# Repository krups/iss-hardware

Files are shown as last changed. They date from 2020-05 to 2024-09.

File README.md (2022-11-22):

# Kentucky RE-entry Probe Experiment 2
Board files, schematics, DXF, BOM, partslist and documentation for the KREPE-2 mission, part of the KRUPS campaign at the University of Kentucky. Documentation PDF can be found [Flight Computer Hardware Manual](doc/krepe-flight-computer-manual.pdf).

Documentation for the KREPE-1 mission can be found on the krepe1 branch [here](https://github.com/krups/iss-hardware/blob/krepe1/doc/krepe-flight-computer-manual.pdf).

### Board renders
<p>
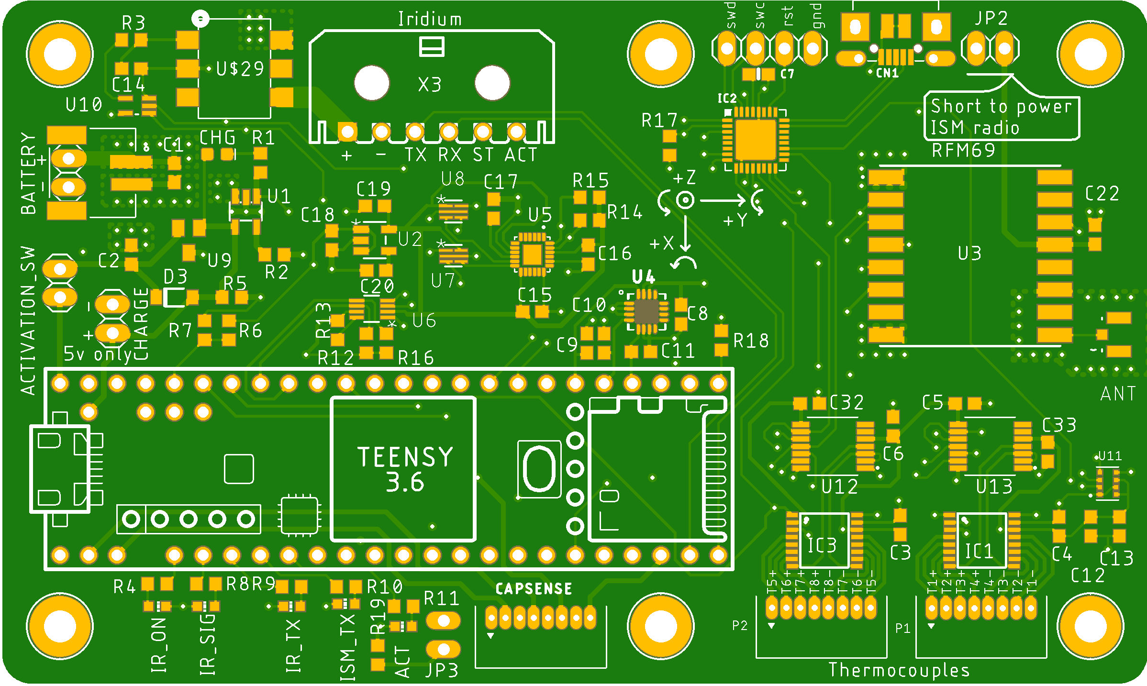
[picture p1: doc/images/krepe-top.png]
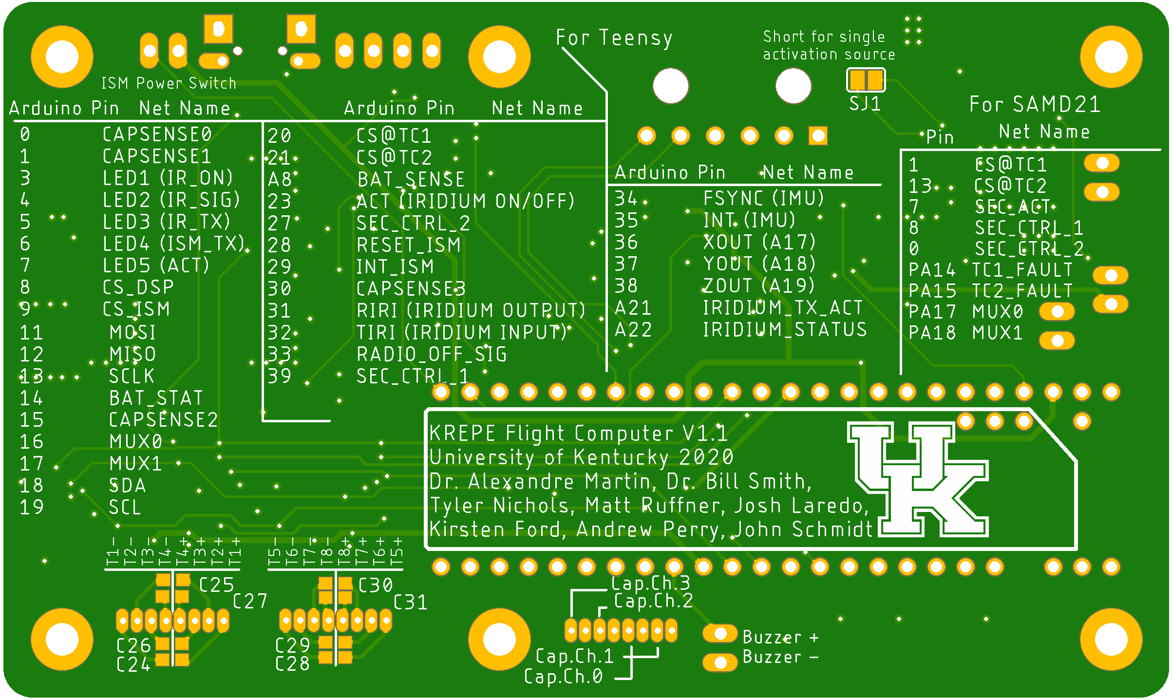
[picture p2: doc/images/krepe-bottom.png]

</p>

### Libraries and datasheets for components
- Thermocouple to digital converter
  -  [MAX31856 Library](https://github.com/adafruit/Adafruit_MAX31856)
  -  [MAX31856 Datasheet](https://datasheets.maximintegrated.com/en/ds/MAX31856.pdf)
- Analog Multiplexer
  - [ADG609BRUZ datasheet](https://www.analog.com/media/en/technical-documentation/data-sheets/ADG608_609.pdf)
- Debug Radio
  - [RFM69HCW](https://www.digikey.com/product-detail/en/sparkfun-electronics/COM-13909/1568-1394-ND/6023504)
- 9-axis IMU
  - [DPE Library](https://github.com/drcpattison/DPEng_ICM20948_AK09916)
  - [Sparkfun Library](https://github.com/sparkfun/SparkFun_ICM-20948_ArduinoLibrary)
  - [Datasheet](https://www.invensense.com/wp-content/uploads/2016/06/DS-000189-ICM-20948-v1.3.pdf)
- Solid state relay
  - [Datasheet](https://www.digikey.com/product-detail/en/panasonic-electric-works/AQV252GAX/255-3375-1-ND/2810282)
- High G Accelerometer
  - [Datasheet](https://www.digikey.com/product-detail/en/analog-devices-inc/ADXL377BCPZ-RL7/ADXL377BCPZ-RL7CT-ND/3678489)
- Safety Co-processor
  - [Datasheet](https://www.digikey.com/product-detail/en/microchip-technology/ATSAMD21E16B-MFT/ATSAMD21E16B-MFTCT-ND/5455793)
  - [Arduino variant reference](https://github.com/adafruit/ArduinoCore-samd/blob/master/variants/trinket_m0/variant.cpp)
 
### Teensy pin assignments wrt. to Arduino 

| Teensy Arduino Pin | Net Name | Notes |
|---|---|---|
| 0 | CAPSENSE 1 |  input, read with ```touchRead(pin)``` |
| 1 | CAPSENSE 0 |  input, read with ```touchRead(pin)``` |
| 3 | LED IRIDIUM ON |  active high |
| 4 | LED IRIDIUM SIGNAL_OK | active high |
| 5 | LED IRIDIUM TRANSMITTING | active high |
| 6 | LED ISM TRANSMITTING | active high |
| 7 | LED ACTIVITY | active high |
| 8			  | CS_DSP		 | active low chip select for DSP310 pressure sensor |
| 9 | CS_ISM | rfm69 chip select |
| 11 | MOSI | |
| 12 | MISO | |
| 13 | SCLK | |
| 14 | BAT_STAT | high when charging |
| 15 | CAPSENSE2 | input, read with ```touchRead(pin)``` |
| 16 | MUX0 | output to analog mux |
| 17 | MUX1 | output to analog mux |
| 18 | SDA | |
| 19 | SCL | |
| 20 | CS@TC1 |  U12 chip select |
| 21 | CS@TC2 |  U13 chip select |
| A8 | BAT SENSE | (A8)  halved by voltage divider |
| 23 | PRI ACT | output to iridium activation 'AND' gate  |
| 24 | BUZZER | buzzer output |
| 25 | TC1 FAULT | (ACTIVE LOW) |
| 26 | TC2 FAULT | (ACTIVE LOW) |
| 27 | SEC CTRL 2 | i/o to safety processor |
| 28 | RESET ISM |  reset to rfm69 |
| 28 | INT ISM |  interrupt from rfm69 |
| 30 | CAPSENSE3 |  input, read with ```touchRead(pin)``` |
| 31 | RIRI | (IRIDIUM OUTPUT) |
| 32 | TIRI | (IRIDIUM INPUT)  |
| 33 | RADIO OFF SIG | pulled high when 3.3v to ism radio is present |
| 34 | FSYNC | IMU sync signal (not necessary for functionality) |
| 35 | INT | IMU interrupt pin (not necessary for functionality) |
| 36 | XOUT | (A17)  high g accel output |
| 37 | YOUT | (A18)  high g accel output |
| 38 | ZOUT | (A19)  high g accel output |
| 39 | SEC CTRL 1 | i/o to safety processor |
| A21 | IRIDIUM TX ACT | iridium output indicating the module is actively transmitting RF |
| A22 | IRIDIUM STATUS |  iridium output indicating an SBD message has arrived |

### Safety processor pin assignments wrt. to Arduino 

The last four pins for the safety processor will need to be added into the board variant file for the trinket m0 since only 5 pins are mapped to physical pads on the current m0 variant.cpp file (or we can make our own arduino board support package ;) )

```SEC CTRL 1``` and ```SEC CTRL 1``` are to be used to coordinate use of the SPI bus so that both the Teensy and safety processor do not drive bus lines to opposite logic levels.

| Safety Processor Arduino Pin|   Net Name                       |                 Note |
|-------------------------|--------------------------|------------------|
| 1                       | CS@TC1                   |    also connected to teensy GPIO              |
| 13                      | CS@TC2                   |    also connected to teensy GPIO              |
| 7                       | SEC ACT                  |     output to activation 'AND' gate             |
| 8                       | SEC CTRL 1               |  i/o with teensy                |
| 0                       | SEC CTRL 2               |  i/o with teensy                |
| PA14                    | TC1 FAULT                |         input        |
| PA15                    | TC2 FAULT                |    input            |
| PA17                    | MUX0                     |       need to use i/o with teensy to avoid collisions on SPI bus           |
| PA18                    | MUX1                     |        need to use i/o with teensy to avoid collisions on SPI bus         |

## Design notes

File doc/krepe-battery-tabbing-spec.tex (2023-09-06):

\documentclass{article}
\usepackage[utf8]{inputenc}

\title{KREPE2 Battery Tabbing Process Specification and Acceptance Testing}
\author{Matt Ruffner, Kirsten Ford}
\date{}

\usepackage{url}
\usepackage{float}
\usepackage{tikz}
\usepackage{natbib}
\usepackage{graphicx}
\usepackage{listings}
\usepackage{subcaption}
\usepackage{fullpage}
\usepackage{hyperref}
\usepackage{pdfpages}
\hypersetup{
    colorlinks=true,
    linkcolor=blue,
    filecolor=magenta,      
    urlcolor=cyan,
}

\begin{document}

\maketitle
\tableofcontents
\listoffigures
\listoftables
\newpage

%%%%%%%%%%%%%%%%%%%%%%%%%%%%%%%%%%%%%%%%%%%%%%%%%%%%%%%%%%%%%%%%%%%%%%%%%%%%%%%%%%%%%%%%%
%%%%%%%%%%%%%%%%%%%%%%%%%%%%%%%%%%%%%%%%%%%%%%%%%%%%%%%%%%%%%%%%%%%%%%%%%%%%%%%%%%%%%%%%%
%%%%%%%%%%%%%%%%%%%%%%%%%%%%%%%%%%%%%%%%%%%%%%%%%%%%%%%%%%%%%%%%%%%%%%%%%%%%%%%%%%%%%%%%%
%%%%%%%%%%%%%%%%%%%%%%%%%%%%%%%%%%%%%%%%%%%%%%%%%%%%%%%%%%%%%%%%%%%%%%%%%%%%%%%%%%%%%%%%%
\section{Introduction}
This document outlines the procedures and verifications done to ensure the integrity of the spot welds used to attach tabs to the 18650 cells for the KREPE-2 mission. The procedures and specifications in this documents have been written to adhere to the guidelines of NASA battery tabbing and specification document \textit{\textbf{PRC-0009 Rev. D}}. According to this document, ``A Welding Procedure Specification (WPS) shall be qualified for each unique weld type to be produced by conforming to the requirements below, before the production welds are made." The WPS for tabbing the KREPE-2 batteries is defined in the following section. 

\section{Battery Acceptance Testing}

1 minute per axis

used spectrum that was already qualified by JSC document, help with reflight

Batteries were vibration tested at Yokohama facilities at the cell level on each axis. Capacity and open circuit voltage (OCV) were recorded before (see Tab. \ref{tab:acc1}) and after testing (see Tab. \ref{tab:acc2}) to ensure no cells were damaged during vibration. Six cells can be seen on the shaker table in the cell mounting form in Fig. \ref{fig:cell-setup}.

\begin{figure}[H]
\centering
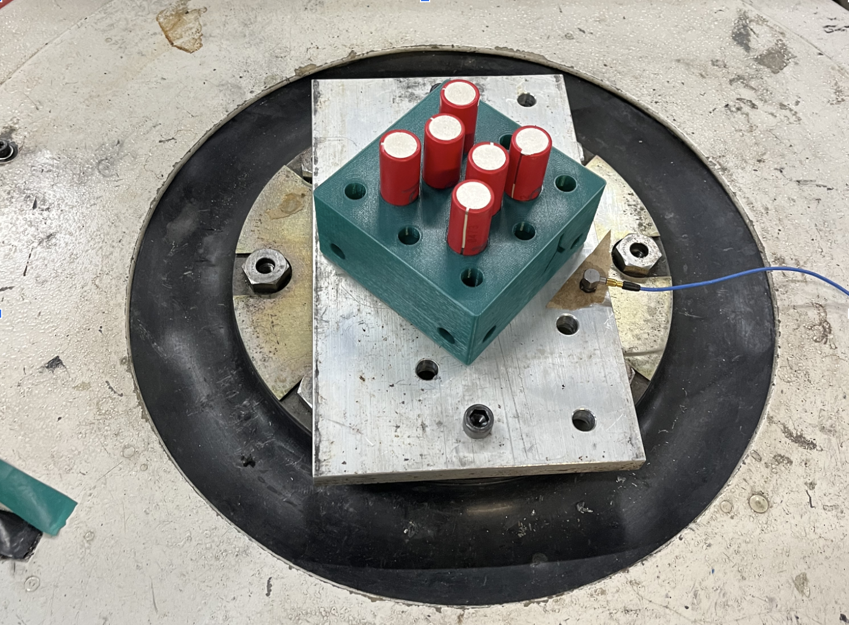
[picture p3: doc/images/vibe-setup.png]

\caption{Six cells in the 3D printed battery holder, mounted to the Yokohama shaker table.}
\label{fig:cell-setup}
\end{figure}

\begin{table}[H]
    \centering
    \caption{Capacity and voltage measurements made before vibration testing.}
    \begin{tabular}{llll}
        \textbf{Cell \#} & \textbf{OCV before vibe (V)} & \textbf{Capacity before vibe (mAh)} & \textbf{Pass vibe visual inspection? y/n} \\ \hline
        1 & 4.14 & 3138 & y \\ 
        2 & 4.15 & 3100 & y \\ 
        3 & 4.15 & 3151 & y \\ 
        4 & 4.14 & 3132 & y \\ 
        5 & 4.16 & 3124 & y \\ 
        6 & 4.16 & 3099 & y \\ 
        7 & 4.14 & 3109 & y \\ 
        8 & 4.14 & 3091 & y \\ 
        9 & 4.15 & 3159 & y \\ 
        10 & 4.14 & 3148 & y \\ 
        11 & 4.17 & 3123 & y \\ 
        12 & 4.17 & 3102 & y \\ 
        13 & 4.13 & 3093 & y \\ 
        14 & 4.14 & 3091 & y \\ 
        15 & 4.15 & 3139 & y \\ 
        16 & 4.15 & 3158 & y \\ 
        17 & 4.17 & 3111 & y \\ 
        18 & 4.17 & 3103 & y \\ 
        19 & 4.13 & 3107 & y \\ 
        20 & 4.13 & 3110 & y \\ 
        21 & 4.14 & 3095 & y \\ 
        22 & 4.13 & 3116 & y \\ 
        23 & 4.15 & 3169 & y \\ 
        24 & 4.15 & 3141 & y \\ 
        25 & 4.15 & 3161 & y \\ 
        26 & 4.15 & 3162 & y \\ 
        27 & 4.17 & 3117 & y \\ 
        28 & 4.17 & 3109 & y \\ 
        29 & 4.17 & 3099 & y \\ 
        30 & 4.17 & 3126 & y \\ 
        31 & 4.14 & 3096 & y \\ 
        32 & 4.14 & 3065 & y \\ 
        33 & 4.14 & 3102 & y \\ 
        34 & 4.14 & 3119 & y \\ 
        35 & 4.15 & 3153 & y \\ 
        36 & 4.15 & 3142 & y \\ 
    \end{tabular}
    \label{tab:acc1}
\end{table}

\begin{table}[H]
    \centering
    \caption{Capacity and voltage measurements after vibration testing. The differences in measured capacity from before and after vibration shows that all cells passed the acceptance test.}
    \begin{tabular}{lllll}
        \textbf{Cell \#} & \textbf{OCV after vibe (V)} & \textbf{Capacity after vibe (mAh)} & \textbf{\%diff OCV} & \textbf{\%diff capacity} \\ \hline
        1 & 4.15 & 3117 & 0\% & 1\% \\ 
        2 & 4.15 & 3110 & 0\% & 0\% \\ 
        3 & 4.15 & 3108 & 0\% & 1\% \\ 
        4 & 4.14 & 3163 & 0\% & -1\% \\ 
        5 & 4.16 & 3191 & 0\% & -2\% \\ 
        6 & 4.16 & 3179 & 0\% & -3\% \\ 
        7 & 4.14 & 3169 & 0\% & -2\% \\ 
        8 & 4.14 & 3168 & 0\% & -2\% \\ 
        9 & 4.15 & 3123 & 0\% & 1\% \\ 
        10 & 4.15 & 3124 & 0\% & 1\% \\ 
        11 & 4.17 & 3111 & 0\% & 0\% \\ 
        12 & 4.17 & 3114 & 0\% & 0\% \\ 
        13 & 4.14 & 3125 & 0\% & -1\% \\ 
        14 & 4.14 & 3183 & 0\% & -3\% \\ 
        15 & 4.14 & 3131 & 0\% & 0\% \\ 
        16 & 4.15 & 3142 & 0\% & 1\% \\ 
        17 & 4.17 & 3141 & 0\% & -1\% \\ 
        18 & 4.17 & 3121 & 0\% & -1\% \\ 
        19 & 4.14 & 3103 & 0\% & 0\% \\ 
        20 & 4.13 & 3121 & 0\% & 0\% \\ 
        21 & 4.14 & 3168 & 0\% & -2\% \\ 
        22 & 4.14 & 3140 & 0\% & -1\% \\ 
        23 & 4.15 & 3101 & 0\% & 2\% \\ 
        24 & 4.15 & 3132 & 0\% & 0\% \\ 
        25 & 4.15 & 3146 & 0\% & 0\% \\ 
        26 & 4.15 & 3141 & 0\% & 1\% \\ 
        27 & 4.17 & 3161 & 0\% & -1\% \\ 
        28 & 4.17 & 3164 & 0\% & -2\% \\ 
        29 & 4.17 & 3168 & 0\% & -2\% \\ 
        30 & 4.17 & 3176 & 0\% & -2\% \\ 
        31 & 4.14 & 3180 & 0\% & -3\% \\ 
        32 & 4.14 & 3154 & 0\% & -3\% \\ 
        33 & 4.14 & 3111 & 0\% & 0\% \\ 
        34 & 4.14 & 3118 & 0\% & 0\% \\ 
        35 & 4.15 & 3105 & 0\% & 2\% \\ 
        36 & 4.15 & 3114 & 0\% & 1\% \\ 
    \end{tabular}
    \label{tab:acc2}
\end{table}

\section{Welding Process Specification}

\subsection{Equipment}

The battery welder used is a kit welder\footnote{\url{https://malectrics.eu/product/diy-arduino-battery-spot-welder-prebuilt-kit-v3/}} powered by a 12000mAh 3S LiPo battery. The full welding setup including battery, weld controller, and probes can be seen in Fig.~\ref{fig:welder}. Detailed information about the welding equipment is shown in Table~\ref{tab:weldequip}. 

Not every detail from the \textit{\textbf{PRC-0009 Rev. D}} spec is able to be replicated with this setup, including the ability to measure the down force of the probes on to working surface. In order to make sure that the welds stay consistent, a \textit{trained hand} method is used. This ensures that the person performing the resistance spot welds on the flight cells is the same person performing the welds for the weld process verification. In both scenarios this person is Matt Ruffner.

\begin{figure}[h!]
\centering

\caption{Battery tab welding equipment. Battery (left) attaches to the weld controller (center) and allows weld parameters to be changed for use with the welding probes (right).}
\label{fig:welder}
\end{figure}

\begin{table}
\centering
\caption{Resistance spot welding weld schedule}
\label{tab:weldequip}
\begin{tabular}{|l l|}
\hline
\multicolumn{2}{|l|}{\textbf{Equipment Identification}} \\
Owner / location &  KRUPS, RGAN 110 \\
Power supply & MaxAmps 3S 12000 mAh LiPo \\
Weld controller serial number & sw-pbkit-v4 \\
Weld head / model & SeeSii 2021 \\
Interconnecting cable & 8 AWG, 6 in \\
&\\
\hline
\multicolumn{2}{|l|}{\textbf{Battery}} \\
Manufacturer & Sanyo \\
Type / size & NCR18650B-H07XA \\
Material type & Lithium ion battery \\
&\\
\hline
\multicolumn{2}{|l|}{\textbf{Connecting Material}} \\
Manufacturer & SeeSii \\
Type & Nickel \\
Thickness / width & 1.5"L x 0.355"W x 0.005"T \\
&\\
\hline
\multicolumn{2}{|l|}{\textbf{Electrodes}} \\
Manufacturer & SeeSii \\
Material & Copper \\
Distance between electrode tips & 0.2 in \\
Contact tip surface shape & round \\
Electrode tip size & 0.059 in. diameter\\
&\\
\hline
\multicolumn{2}{|l|}{\textbf{Welding electrode configuration and setup}} \\
Number of pulses &  1 \\
%Squeeze time      & 1 second \\
%Upslope duration & N/A \\
Pulse duration & 10 ms \\
%Downslope & 0 ms \\
%Hold time & 500 ms \\
%Negative Electrode Force &1 lbs \\
%Positive Electrode Force &1 lbs\\
%Pull force & ??\\
\hline
\end{tabular}
\end{table}

\subsection{Process}

say certified operator instead of trained hand

add reference to section 4 table

A tab weld consists of two separate weld instances, yielding 4 weld points, or ``nuggets", on each tab. There are two types of packs required for this mission. The 3S1P pack requires standard tab-to-battery welds, while the 1S3P pack requires tab-to-battery welds as well as tab-to-tab welds.

To qualify both of these processes, plug pull out tests will be done for tabs attached to other tabs and tabs attached to batteries. In both scenarios, success is determined by plug pullout, signifying that the weld is indeed stronger than the original material by itself.

\begin{enumerate}
\item Cut 4 pieces of tab material 1.5" long
\item Mark 4 points 0.2 in apart to weld at on each tab
\item Ensure the battery powering the welder is charged and its voltage is greater than 11.1 V
\item Initialize the weld controller and select 10ms weld pulse duration
\item Stabilize the battery and pin the tab with one electrode
\item Press the other weld tip to the battery
\item Repeat weld for second weld on a given tab. 
\end{enumerate}

\section{Weld Verification}

change language to "it can be seen"

As per PRC-0009, 15 sets of example welds are the minimum test batch size. To this end, tabs were attached to both the positive and negative ends of two Sanyo cells. There are 16 total welds resulting (in groups of 4 spot welds for each tab attachment point).

Figure~\ref{fig:stabilized-tab} shows a tab sitting on top of the first cell, prior to tabbing. After this, 4 points were marked on the tab to indicated where the welds were to be placed. After the markings are placed, the weld tips are pressed to the tab with a moderate amount of force by hand. The weld controller senses this connection and triggers a weld 4 seconds after the tips are touched to the tab. After both welds have been done on a single tab (producing 4 weld nuggets), the tab looks like that shown in Fig.~\ref{fig:post-weld}.

\begin{figure}[h]
\centering

\caption{Nickel tab stabilized on top to cell prior to welding.}
\label{fig:stabilized-tab}
\end{figure}

\begin{figure}[h]
\centering
\begin{subfigure}{0.6\textwidth}

\caption{After both welds have been performed on the tab. You can see the silver sharpie locater markings underneath the weld to help guide the placement of the weld tips during the welding process.}
\label{fig:post-weld}
\end{subfigure}
\hfill
\begin{subfigure}{0.3\textwidth}

\caption{Pliers were used to pull the welded tab off of the battery at a right angle to the surface of the weld.}
\label{fig:pull-config}
\end{subfigure}
\caption{Result of resistance spot welding using our weld controller and the configuration of the destructive peel test.}
\end{figure}

After all 4 tabs are attached to the two cells with a total of 16 weld nuggets, the peel test proceeds. The peel test consists of holding the cell in the upright position and using a pair of pliers to pull the tab at a 90 degree angle to the working surface (the plane of the welds). This configuration is shown in Fig.~\ref{fig:pull-config}.

Using this configuration, the destructive peel test continued. The tabs were pulled at right angles until the tab cam free from the battery. The results of the 4 peel tests are shown in Figs.~\ref{fig:peel-1}, \ref{fig:peel-2}, \ref{fig:peel-3}, and \ref{fig:peel-4}. As you can see, all 16/16 weld nuggets proved stronger than the tab, and the 4 peel tests resulted in 100\% plug pullout. 

\begin{figure}[H]
\centering

\begin{subfigure}{0.3\textwidth}

\caption{Tab 1, test cell 1.}
\label {fig:peel-1}
\end{subfigure}
\hfill
\begin{subfigure}{0.3\textwidth}

\caption{Tab 2, test cell 1.}
\label {fig:peel-2}
\end{subfigure}
\\
\begin{subfigure}{0.3\textwidth}
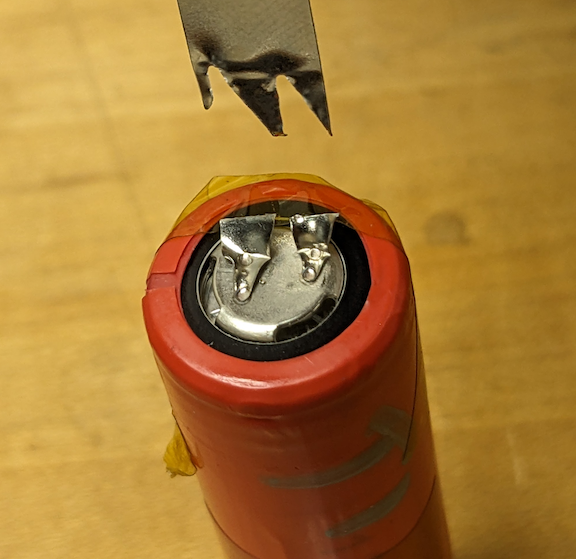
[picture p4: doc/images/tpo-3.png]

\caption{Tab 1, test cell 2.}
\label {fig:peel-3}
\end{subfigure}
\hfill
\begin{subfigure}{0.3\textwidth}
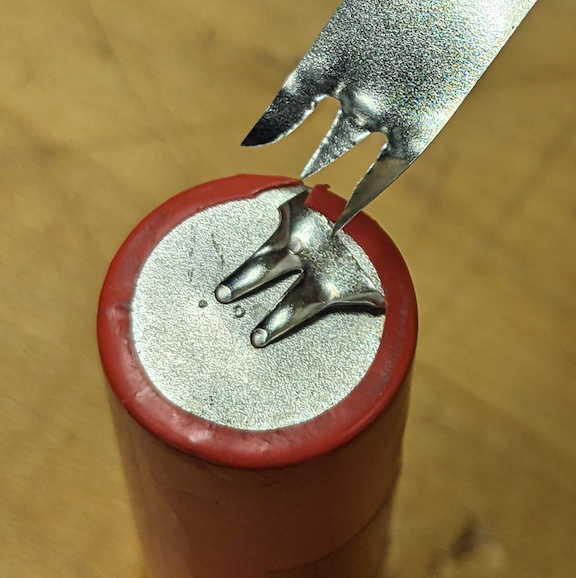
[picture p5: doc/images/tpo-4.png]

\caption{Tab 2, test cell 2.}
\label {fig:peel-4}
\end{subfigure}
\caption{Results of plug pull out tests on the sample batch of welds.}
\end{figure}

\subsection{Weld Process Verification Summary}
Using the welding setup shown in Fig.~\ref{fig:welder}, 16 weld nuggets were created and tested to destruction with a peel test. For all 16 nuggets, plug pullout occurred. This confirms the strength of the welding process specified in this document.

\section{Battery Tabbing Arrangement}

The KREPE-2 capsules have 2 battery packs with 3 cells each. One is a 3.7V pack with the cells tabbed in parallel, and another 11.1V pack with the cells tabbed in series. Figures \ref{fig:parallel-pack} and \ref{fig:series-pack} show the arrangement of the tabs on the cells for the 3.7V and 11.1V pack, respectively.

\begin{figure}[H]
\centering

\begin{subfigure}{0.45\textwidth}
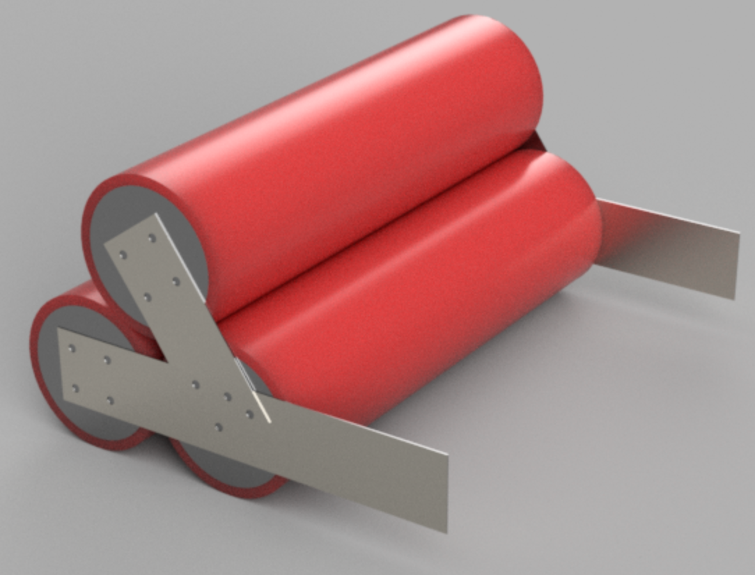
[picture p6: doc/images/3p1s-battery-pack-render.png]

\caption{Rendering of 3.7V 3P1S battery pack}
\label {fig:parallel-pack}
\end{subfigure}
\hfill
\begin{subfigure}{0.45\textwidth}
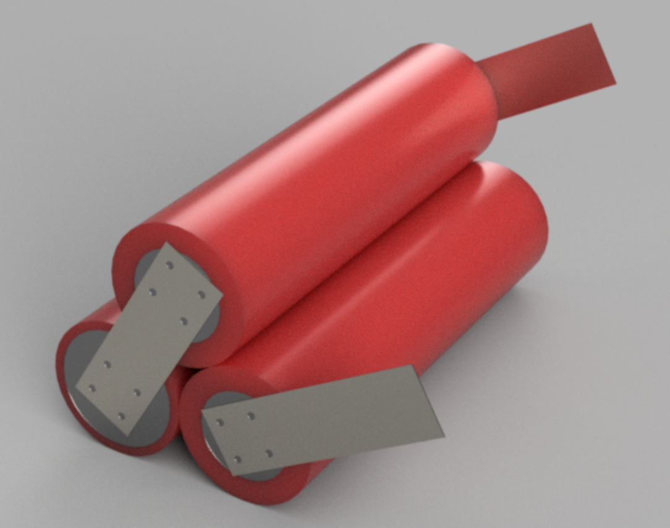
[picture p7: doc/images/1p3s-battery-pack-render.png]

\caption{Rendering of 11.1V 1P3S battery pack}
\label {fig:series-pack}
\end{subfigure}

\end{figure}

The tabbing material is made of nickel strips measuring $0.005$ inches thick and $0.355$ inches wide and cut to length before being attached to the batteries. Dimensional drawings showing weld spacing and tab dimensions for both packs can be found in Figs. \ref{fig:1s3p_drawing} and \ref{fig:3s1p_drawing}.

\appendix

add drawing number

add approval for drawings

\section{Battery Pack Drawings}
Dimensions in inches.
\begin{figure}
\centering

\caption{3S1P pack drawing.}
\label{fig:3s1p_drawing}
\end{figure}

\begin{figure}
\centering

\caption{1S3P pack drawing.}
\label{fig:1s3p_drawing}
\end{figure}

\end{document}

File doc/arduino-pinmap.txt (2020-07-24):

Arduino Pin     Net

Teensy 3.5
0               CAPSENSE0
1               CAPSENSE1
3               LED_IRIDIUM_ON
4               LED_IRIDIUM_SIGNAL_OK
5               LED_IRIDIUM_TRANSMITTING
6               LED_ISM_TRANSMITTING
7               LED_ACTIVITY
8		CS_DSP
9               CS_ISM
11              MOSI
12              MISO
13              SCLK
14              BAT_STAT
15              CAPSENSE2
16              MUX0
17              MUX1
18              SDA
19              SCL
20              CS@TC1
21              CS@TC2
A8              BAT_SENSE (A8)
23              PRI_ACT (IRIDIUM ON/OFF)
24              BUZZER
25              TC1_FAULT (ACTIVE LOW)
26              TC2_FAULT (ACTIVE LOW)
27              SEC_CTRL_2
28              RESET_ISM
28              INT_ISM
30              CAPSENSE3
31              RIRI (IRIDIUM OUTPUT)
32              TIRI (IRIDIUM INPUT)
33              RADIO_OFF_SIG
34              FSYNC (IMU)
35              INT (IMU)
36              XOUT (A17)
37              YOUT (A18)
38              ZOUT (A19) 
39              SEC_CTRL_1        
A21             IRIDIUM_TX_ACT
A22             IRIDIUM_STATUS

Safety Processor (ATSAMD21E16B)
1               CS@TC1
13              CS@TC2
7               SEC_ACT
8               SEC_CTRL_1
0               SEC_CTRL_2
PA14            TC1_FAULT
PA15            TC2_FAULT
PA17            MUX0
PA18            MUX1

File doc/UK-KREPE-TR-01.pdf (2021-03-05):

# UK-KREPE-TR-01

Matt Ruffner
2/12/2021

Verification of battery protection circuitry
Functional verification of the battery protection circuitry (BPC) was performed by shorting the battery pack together downstream of the BPC. The results of this test are shown in Fig. 1. The top trace shows the pack voltage prior, during, and after a short circuit scenario. The bottom trace is the current draw from the pack. As you can see, after 6 milliseconds, the BPC engages and cells are disconnected from the output and current draw from the pack drops to zero amps. In addition, a low voltage cutoff test was performed on the KREPE Experiments with the battery protection circuitry in place that verifies electrical systems are disabled when battery voltage reaches less than 3.3 volts.

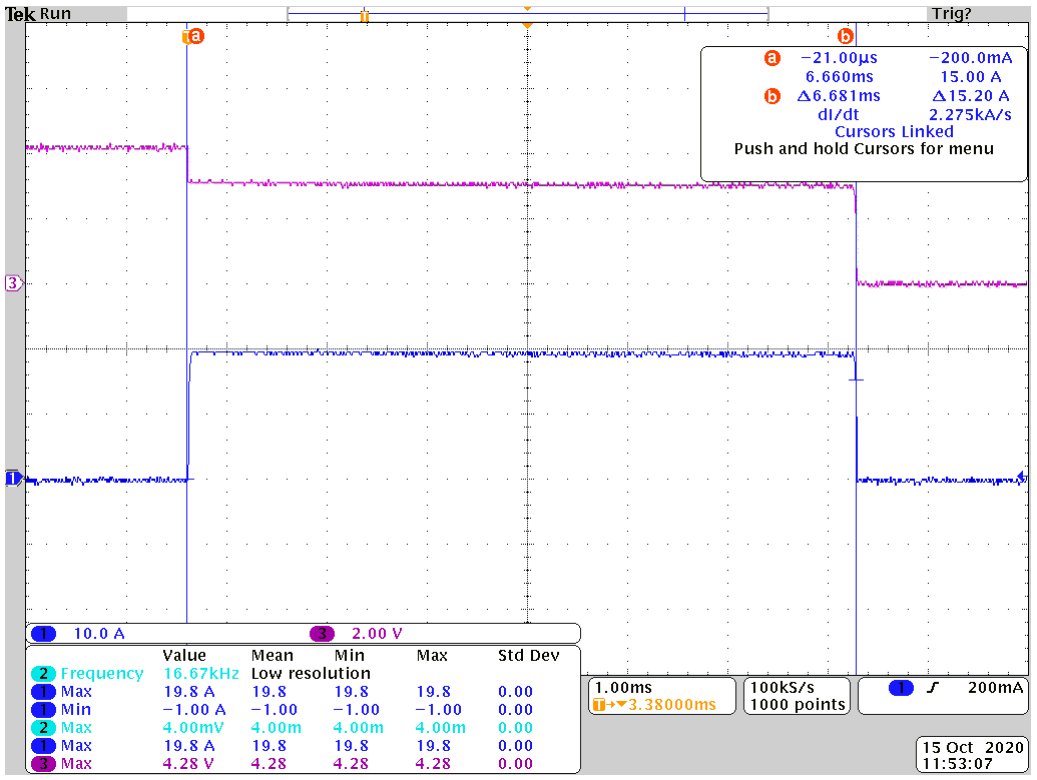
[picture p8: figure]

Figure 1: Overcurrent protection engaging on the battery protection circuitry.

Functional testing before and after vibration
After this initial visual inspection, functional testing was performed before and after vibration testing at MSFC. All KREPE Experiments were tested to ensure that they power up into the dormant state upon removal of the pull tab. The test to ensure a capsule starts and goes into dormant mode consists of pulling the pull-tab and listening for startup beeps. Then, listen for an additional two minutes and ensure no activation beep is detected. In addition to not hearing the activation beep, it was additionally confirmed that the capsules did not activate because no iridium packets were received.

Table 1: Functional test before vibe
Part # | Serial # | Date | Pass/Fail | Initial
KREPE-001 | 001 | 1/30/2021 10:44 EST | PASS | MR
KREPE-001 | 002 | 1/30/2021 10:51 EST | PASS | MR
KREPE-002 | N/A | 1/30/2021 11:11 EST | PASS | MR

Table 2: Functional test after vibe
Part # | Serial # | Date | Pass/Fail | Initial
KREPE-001 | 001 | 2/4/2021 15:37 EST | PASS | MR
KREPE-001 | 002 | 2/4/2021 10:51 EST | PASS | MR
KREPE-002 | N/A | 2/4/2021 11:00 EST | PASS | MR

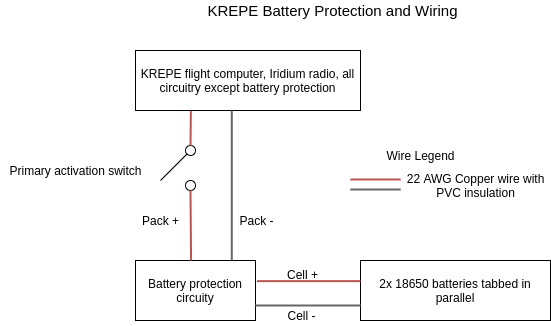
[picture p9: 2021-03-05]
doc/images/krepe-electrical-overview.png

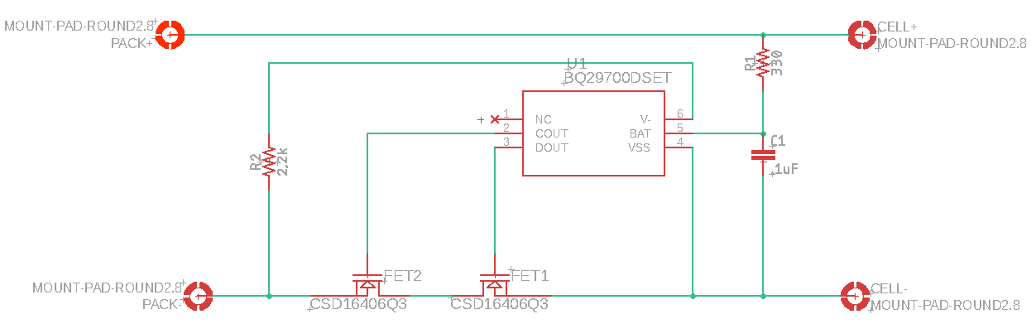
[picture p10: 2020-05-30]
doc/images/battery_protection_schematic.png

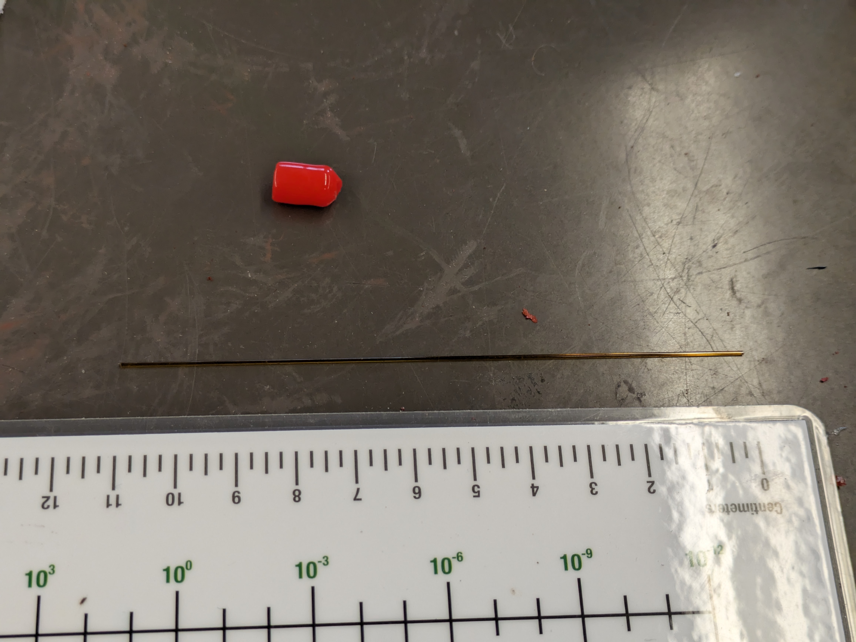
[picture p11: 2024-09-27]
doc/images/krepe2build/spectrometer4.jpg

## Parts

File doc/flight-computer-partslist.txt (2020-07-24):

Partlist

Exported from flight-computer.sch at 7/23/20 8:11 PM

EAGLE Version 9.6.2 Copyright (c) 1988-2020 Autodesk, Inc.

Assembly variant: 

Part          Value                Device                 Package                   Library                 Sheet

ACTIVATION_SW                      PINHD-1X2              1X02                      pinhead                 3
ANT           U.FL-R-SMT-1(10)     U.FL-R-SMT-1(10)       CONN_R-SMT-1(10)          ufl                     4
BATTERY       2 PIN JST            S2B-PH-SM4-TB(LF)(SN)  JST_S2B-PH-SM4-TB(LF)(SN) S2B-PH-SM4-TB_LF__SN_   3
C1            10uF                 C-EUC0603              C0603                     rcl                     3
C2            1uF                  C-EUC0603              C0603                     rcl                     3
C3            0.1uF                C-USC0603              C0603                     adafruit                2
C4            0.1uF                C-USC0603              C0603                     adafruit                2
C5            0.1uF                C-USC0603              C0603                     adafruit                2
C6            0.1uF                C-USC0603              C0603                     adafruit                2
C7            1uF                  CAP_CERAMIC0603_NO     0603-NO                   microbuilder            5
C8            10uF                 C-USC0603              C0603                     adafruit                1
C9            0.01uF               C-USC0603              C0603                     adafruit                1
C10           0.01uF               C-USC0603              C0603                     adafruit                1
C11           0.01uF               C-USC0603              C0603                     adafruit                1
C12           0.1uF                C-EUC0603              C0603                     rcl                     4
C13           0.1uF                C-EUC0603              C0603                     rcl                     4
C14           0.1uF                C-USC0603              C0603                     adafruit                3
C15           0.1uF                C-EUC0603              C0603                     rcl                     1
C16           0.1uF                C-EUC0603              C0603                     rcl                     1
C17           0.1uF                C-EUC0603              C0603                     rcl                     1
C18           0.1uF                C-USC0603              C0603                     rcl                     3
C19           2.2uF                C-USC0603              C0603                     rcl                     3
C20           0.01uF               C-USC0603              C0603                     rcl                     3
C22           1uF                  C-EUC0603              C0603                     rcl                     4
C24           0.01uF               C-USC0603              C0603                     adafruit                2
C25           0.01uF               C-USC0603              C0603                     adafruit                2
C26           0.01uF               C-USC0603              C0603                     adafruit                2
C27           0.01uF               C-USC0603              C0603                     adafruit                2
C28           0.01uF               C-USC0603              C0603                     adafruit                2
C29           0.01uF               C-USC0603              C0603                     adafruit                2
C30           0.01uF               C-USC0603              C0603                     adafruit                2
C31           0.01uF               C-USC0603              C0603                     adafruit                2
C32           0.1uF                C-USC0603              C0603                     adafruit                2
C33           0.1uF                C-USC0603              C0603                     adafruit                2
CAPSENSE      53048-0810           53048-0810             53048-0810                con-molex-picoblade     4
CHARGE                             PINHD-1X2              1X02                      pinhead                 3
CHG           RED                  LED-RED0603            LED-0603                  SparkFun-LED            3
CN1           4U#20329             USB_MICRO_20329_V2     4UCONN_20329_V2           microbuilder            5
D3            MBR120               MBR120                 SOD123FL                  gsynth                  3
H1            MOUNT-PAD-ROUND2.8   MOUNT-PAD-ROUND2.8     2,8-PAD                   holes                   1
H2            MOUNT-PAD-ROUND2.8   MOUNT-PAD-ROUND2.8     2,8-PAD                   holes                   1
H3            MOUNT-PAD-ROUND2.8   MOUNT-PAD-ROUND2.8     2,8-PAD                   holes                   1
H4            MOUNT-PAD-ROUND2.8   MOUNT-PAD-ROUND2.8     2,8-PAD                   holes                   1
H5            MOUNT-PAD-ROUND2.8   MOUNT-PAD-ROUND2.8     2,8-PAD                   holes                   1
H6            MOUNT-PAD-ROUND2.8   MOUNT-PAD-ROUND2.8     2,8-PAD                   holes                   1
IC1           ADG609RU             ADG609RU               TSSOP16                   analog-devices          2
IC2           ATSAMD21E            ATSAMD21E              QFN32_5MM                 microbuilder            5
IC3           ADG609RU             ADG609RU               TSSOP16                   analog-devices          2
JP1                                PINHD-1X4              1X04                      pinhead                 5
JP2                                PINHD-1X2              1X02                      pinhead                 3
JP3                                PINHD-1X2              1X02                      pinhead                 4
LED1                               LEDCHIP-LED0603        CHIP-LED0603              adafruit                4
LED2                               LEDCHIP-LED0603        CHIP-LED0603              adafruit                4
LED3                               LEDCHIP-LED0603        CHIP-LED0603              adafruit                4
LED4                               LEDCHIP-LED0603        CHIP-LED0603              adafruit                4
LED5                               LEDCHIP-LED0603        CHIP-LED0603              adafruit                4
P1            53048-0810           53048-0810             53048-0810                con-molex-picoblade     2
P2            53048-0810           53048-0810             53048-0810                con-molex-picoblade     2
R1            1k                   R-US_R0603             R0603                     rcl                     3
R2            2.2k                 R-US_R0603             R0603                     rcl                     3
R3            288                  R-US_R0603             R0603                     adafruit                3
R4            470                  R-US_R0603             R0603                     rcl                     4
R5            100k                 R-US_R0603             R0603                     rcl                     3
R6            100k                 R-US_R0603             R0603                     rcl                     3
R7            100k                 R-US_R0603             R0603                     rcl                     3
R8            470                  R-US_R0603             R0603                     rcl                     4
R9            470                  R-US_R0603             R0603                     rcl                     4
R10           470                  R-US_R0603             R0603                     rcl                     4
R11           470                  R-US_R0603             R0603                     rcl                     4
R12           2.2k                 R-US_R0603             R0603                     rcl                     1
R13           200k                 R-US_R0603             R0603                     rcl                     1
R14           2.2k                 R-US_R0603             R0603                     rcl                     1
R15           2.2k                 R-US_R0603             R0603                     rcl                     1
R16           2.2k                 R-US_R0603             R0603                     rcl                     1
R17           10k                  R-US_R0603             R0603                     rcl                     5
R18           100k                 R-US_R0603             R0603                     rcl                     3
R19           100                  R-US_R0603             R0603                     rcl                     4
SJ1                                SJ                     SJ                        jumper                  5
U$1           TEENSY_3.5/3.6_BASIC TEENSY_3.5/3.6_BASIC   TEENSY_3.5/3.6_BASIC      Teensy356               1
U$29          AQV252GA             AQV252GA               DIP6                      TI_radio                3
U1            MCP73831/OT          MCP73831/OT            SOT23-5L                  adafruit                3
U2            LP2985IM5-1.8/NOPB   LP2985IM5-1.8/NOPB     MF05A                     gsynth                  3
U3            COM-13909            COM-13909              MOD_COM-13909             COM-13909               4
U4            ADXL377              ACCEL_ADXL377          LFCSP16_LQ                microbuilder            1
U5            ICM-20948            ICM-20948              QFN40P300X300X105-25N     ICM-20948               1
U6            PCA9306DCUR          PCA9306DCUR            DCU8                      gsynth                  1
U7            SN74LVC1T45DRLR      SN74LVC1T45DRLR        DRL6                      gsynth                  1
U8            SN74LVC1T45DRLR      SN74LVC1T45DRLR        DRL6                      gsynth                  1
U9            DMP3099L             DMP3099L               SOT23                     gsynth                  3
U10           SN74LVC1G08DCKR      SN74LVC1G08DCKR        SOT65P210X110-5N          SN74LVC1G08DCKR         5
U11           DPS310XTSA1          DPS310XTSA1            XDCR_DPS310XTSA1          DPS310XTSA1             4
U12           MAX31856MUD+         MAX31856MUD+           SOP65P640X110-14N         MAX31856                2
U13           MAX31856MUD+         MAX31856MUD+           SOP65P640X110-14N         MAX31856                2
VBAT_PTH                           PINHD-1X2              1X02                      pinhead                 3
X3                                 HEADER_POS6_43650-0600 43650-0600                con-molex-micro-fit-3_0 3

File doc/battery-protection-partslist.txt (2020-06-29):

Partlist

Exported from BatteryProtection.sch at 6/27/20 10:18 AM

EAGLE Version 9.6.2 Copyright (c) 1988-2020 Autodesk, Inc.

Assembly variant: 

Part     Value              Device                    Package  Library             Sheet

 C1       .1uF               0.33UF/330NF-0805-50V-10% 0805     SparkFun-Capacitors 1
CELL+    MOUNT-PAD-ROUND2.8 MOUNT-PAD-ROUND2.8        2,8-PAD  holes               1
CELL-    MOUNT-PAD-ROUND2.8 MOUNT-PAD-ROUND2.8        2,8-PAD  holes               1
 FET1     CSD16406Q3         CSD16406Q3                DQG0008A KRUPS               1
 FET2     CSD16406Q3         CSD16406Q3                DQG0008A KRUPS               1
PACK+    MOUNT-PAD-ROUND2.8 MOUNT-PAD-ROUND2.8        2,8-PAD  holes               1
PACK-    MOUNT-PAD-ROUND2.8 MOUNT-PAD-ROUND2.8        2,8-PAD  holes               1
 R1       330                33KOHM-0603-1/10W-1%      0603     SparkFun-Resistors  1
 R2       2.2k               33KOHM-0603-1/10W-1%      0603     SparkFun-Resistors  1
 U1       BQ29700DSET        BQ29700DSET               DSE6     KRUPS               1

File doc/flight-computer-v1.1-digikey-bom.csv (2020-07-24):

Manufacturer Part Number | Manufacturer | Digi-Key Part Number | Customer Reference | Reference Designator | Packaging | Part Status | Quantity | Unit Price | Extended Price | Quantity Available | Mfg Std Lead Time | Description | RoHS Status | Lead Free Status | REACH Status
C0603C104Z3VACTU | KEMET | 399-1100-1-ND |  |  | Cut Tape (CT) | Active | 13 | 0.03100 | $0.40 | 1317430 | 8 Weeks | CAP CER 0.1UF 25V Y5V 0603 | ROHS3 Compliant | Lead free | REACH Unaffected
C0603C105K9PACTU | KEMET | 399-7848-1-ND |  |  | Cut Tape (CT) | Active | 3 | 0.10000 | $0.30 | 44304 | 8 Weeks | CAP CER 1UF 6.3V X5R 0603 | ROHS3 Compliant | Lead free | REACH Unaffected
C0603C225K4PACTU | KEMET | 399-7886-1-ND |  |  | Cut Tape (CT) | Active | 1 | 0.14000 | $0.14 | 108108 | 17 Weeks | CAP CER 2.2UF 16V X5R 0603 | ROHS3 Compliant | Lead free | REACH Unaffected
LTST-C191KRKT | Lite-On Inc. | 160-1447-1-ND |  |  | Cut Tape (CT) | Active | 1 | 0.26000 | $0.26 | 185096 | 12 Weeks | LED RED CLEAR SMD | ROHS3 Compliant | Lead free | Not Available
MBR120VLSFT1G | ON Semiconductor | MBR120VLSFT1GOSCT-ND |  |  | Cut Tape (CT) | Active | 1 | 0.44000 | $0.44 | 33932 | 17 Weeks | DIODE SCHOTTKY 20V 1A SOD123FL | ROHS3 Compliant | Lead free | REACH Unaffected
ADG609BRUZ | Analog Devices Inc. | ADG609BRUZ-ND |  |  | Tube | Active | 2 | 6.28000 | $12.56 | 464 | 8 Weeks | IC MULTIPLEXER DUAL 4X1 16TSSOP | ROHS3 Compliant | Lead free | REACH Unaffected
COM-13909 | SparkFun Electronics | 1568-1394-ND |  |  | Bulk | Active | 1 | 5.95000 | $5.95 | 181 | 2 Weeks | RX TXRX MODULE ISM < 1GHZ SMD | RoHS Compliant | Lead free | Not Available
ICM-20948 | TDK InvenSense | 1428-1123-1-ND |  |  | Cut Tape (CT) | Active | 1 | 8.04000 | $8.04 | 52775 | 16 Weeks | IMU ACCEL/GYRO/COMPI2C/SPI 24QFN | ROHS3 Compliant | Lead free | Not Available
U.FL-R-SMT(01) | Hirose Electric Co Ltd | H9161-ND |  |  | Bag | Active | 1 | 1.31000 | $1.31 | 14227 | 12 Weeks | CONN U.FL RCPT STR 50 OHM SMD | RoHS Compliant | Lead free | Not Available
FXP290.07.0100A | Taoglas Limited | 931-1090-ND |  |  | Bag | Active | 0 | 0.00000 | $0.00 | 338 | 8 Weeks | RF ANT 915MHZ FLAT PATCH CAB ADH | ROHS3 Compliant | Lead free | REACH Unaffected
C0603C103M5RACTU | KEMET | 399-7842-1-ND |  |  | Cut Tape (CT) | Active | 12 | 0.03300 | $0.39 | 252300 | 8 Weeks | CAP CER 10000PF 50V X7R 0603 | ROHS3 Compliant | Lead free | REACH Unaffected
0530480810 | Molex | WM1748-ND |  |  | Tray | Active | 3 | 0.55000 | $1.65 | 11857 | 15 Weeks | CONN HEADER R/A 8POS 1.25MM | ROHS3 Compliant | Lead free | REACH Unaffected
RC0603JR-071KL | Yageo | 311-1.0KGRCT-ND |  |  | Cut Tape (CT) | Active | 1 | 0.10000 | $0.10 | 4721429 | 24 Weeks | RES SMD 1K OHM 5% 1/10W 0603 | ROHS3 Compliant | Lead free | REACH Unaffected
RC0603FR-07287RL | Yageo | 311-287HRCT-ND |  |  | Cut Tape (CT) | Active | 1 | 0.10000 | $0.10 | 105967 | 24 Weeks | RES SMD 287 OHM 1% 1/10W 0603 | ROHS3 Compliant | Lead free | REACH Unaffected
RC0603FR-072K2L | Yageo | 311-2.20KHRCT-ND |  |  | Cut Tape (CT) | Active | 5 | 0.10000 | $0.50 | 6504784 | 24 Weeks | RES SMD 2.2K OHM 1% 1/10W 0603 | RoHS Mixed | Lead Mixed | REACH Unaffected
RC0603FR-07470RL | Yageo | 311-470HRCT-ND |  |  | Cut Tape (CT) | Active | 5 | 0.10000 | $0.50 | 2948117 | 24 Weeks | RES SMD 470 OHM 1% 1/10W 0603 | ROHS3 Compliant | Lead free | REACH Unaffected
RC0603JR-07100KL | Yageo | 311-100KGRCT-ND |  |  | Cut Tape (CT) | Active | 4 | 0.10000 | $0.40 | 6379914 | 24 Weeks | RES SMD 100K OHM 5% 1/10W 0603 | ROHS3 Compliant | Lead free | REACH Unaffected
RC0603JR-07200KL | Yageo | 311-200KGRCT-ND |  |  | Cut Tape (CT) | Active | 1 | 0.10000 | $0.10 | 680322 | 24 Weeks | RES SMD 200K OHM 5% 1/10W 0603 | ROHS3 Compliant | Lead free | REACH Unaffected
S2B-PH-SM4-TB(LF)(SN) | JST Sales America Inc. | 455-1749-1-ND |  |  | Cut Tape (CT) | Active | 1 | 0.58000 | $0.58 | 61925 | 16 Weeks | CONN HEADER SMD R/A 2POS 2MM | ROHS3 Compliant | Lead free | REACH Unaffected
AQV252GAX | Panasonic Electric Works | 255-3375-1-ND |  |  | Cut Tape (CT) | Active | 1 | 5.39000 | $5.39 | 16638 | 12 Weeks | SSR RELAY SPST-NO 2.5A 0-60V | RoHS Compliant | Lead free | Not Available
MCP73831T-2ATI/OT | Microchip Technology | MCP73831T-2ATI/OTCT-ND |  |  | Cut Tape (CT) | Active | 1 | 0.56000 | $0.56 | 3910 | 14 Weeks | IC CONTROLLR LI-ION 4.2V SOT23-5 | ROHS3 Compliant | Lead free | REACH Unaffected
LP2985IM5-1.8/NOPB | Texas Instruments | LP2985IM5-1.8/NOPBCT-ND |  |  | Cut Tape (CT) | Active | 1 | 0.76000 | $0.76 | 5109 | 6 Weeks | IC REG LINEAR 1.8V 150MA SOT23-5 | ROHS3 Compliant | Lead free | REACH Unaffected
ADXL377BCPZ-RL7 | Analog Devices Inc. | ADXL377BCPZ-RL7CT-ND |  |  | Cut Tape (CT) | Active | 1 | 11.47000 | $11.47 | 3128 | 14 Weeks | ACCEL 200G ANALOG 16LFCSP | ROHS3 Compliant | Lead free | REACH Unaffected
PCA9306DCUR | Texas Instruments | 296-17988-1-ND |  |  | Cut Tape (CT) | Active | 1 | 0.71000 | $0.71 | 24959 | 8 Weeks | IC TRNSLTR BIDIRECTIONAL 8VSSOP | ROHS3 Compliant | Lead free | REACH Unaffected
SN74LVC1T45DRLR | Texas Instruments | 296-20629-1-ND |  |  | Cut Tape (CT) | Active | 2 | 0.58000 | $1.16 | 28153 | 12 Weeks | IC TRNSLTR BIDIRECTIONAL 6SOT | ROHS3 Compliant | Lead free | REACH Unaffected
DMP3099L-7 | Diodes Incorporated | DMP3099L-7DICT-ND |  |  | Cut Tape (CT) | Active | 1 | 0.33000 | $0.33 | 400163 | 23 Weeks | MOSFET P-CH 30V SOT23 | ROHS3 Compliant | Lead free | REACH Unaffected
0436500600 | Molex | WM1864-ND |  |  | Tray | Active | 1 | 1.64000 | $1.64 | 1065 | 6 Weeks | CONN HEADER R/A 6POS 3MM | ROHS3 Compliant | Lead free | REACH Unaffected
DEV-14055 | SparkFun Electronics | 1568-1443-ND |  |  | Bulk | Active | 1 | 26.25000 | $26.25 | 692 | 8 Weeks | TEENSY 3.5 W/OUT HDRS K64 EVAL | RoHS Compliant | Lead free | Not Available
MAX31856MUD+ | Maxim Integrated | MAX31856MUD+-ND |  |  | Tube | Active | 2 | 6.29000 | $12.58 | 6942 | 8 Weeks | IC CONV THERMOCOUPLE 14TSSOP | ROHS3 Compliant | Lead free | REACH Unaffected
GRM188R61A106KE69J | Murata Electronics | 490-14372-1-ND |  |  | Cut Tape (CT) | Active | 2 | 0.21000 | $0.42 | 268725 | 15 Weeks | CAP CER 10UF 10V X5R 0603 | ROHS3 Compliant | Lead free | Not Available
APTD1608ZGC | Kingbright | 754-1547-1-ND |  |  | Cut Tape (CT) | Active | 5 | 0.59000 | $2.95 | 103295 | 12 Weeks | LED GREEN CLEAR CHIP SMD | ROHS3 Compliant | Lead free | REACH Unaffected
AB1541B-LW100-R | PUI Audio, Inc. | 668-1448-ND |  |  | Bag | Active | 1 | 1.07000 | $1.07 | 31976 | 13 Weeks | BUZZER ELEMENT STD 4.1KHZ 15MM | ROHS3 Compliant | Lead free | Not Available
ATSAMD21E16B-MFT | Microchip Technology | ATSAMD21E16B-MFTCT-ND |  |  | Cut Tape (CT) | Active | 1 | 2.16000 | $2.16 | 9859 | 6 Weeks | IC MCU 32BIT 64KB FLASH 32QFN | ROHS3 Compliant | Lead free | REACH Unaffected
SN74LVC1G08DCKR | Texas Instruments | 296-11602-1-ND |  |  | Cut Tape (CT) | Active | 1 | 0.26000 | $0.26 | 228939 | 6 Weeks | IC GATE AND 1CH 2-INP SC70-5 | ROHS3 Compliant | Lead free | REACH Unaffected
DX4R005JJ2R1800 | JAE Electronics | 670-2675-1-ND |  |  | Cut Tape (CT) | Active | 1 | 0.82000 | $0.82 | 15914 | 14 Weeks | CONN RCPT USB2.0 MICRO B SMD R/A | RoHS Compliant | Lead free | Not Available
DPS310XTSA1 | Infineon Technologies | DPS310XTSA1CT-ND |  |  | Cut Tape (CT) | Active | 1 | 2.89000 | $2.89 | 5209 | 4 Weeks | SENSOR PRESSURE CAPACITIVE | ROHS3 Compliant | Lead free | REACH Unaffected
RC0603FR-07100RL | Yageo | 311-100HRCT-ND |  |  | Cut Tape (CT) | Active | 1 | 0.10000 | $0.10 | 8666777 | 24 Weeks | RES SMD 100 OHM 1% 1/10W 0603 | ROHS3 Compliant | Lead free | REACH Unaffected
RC0603FR-0710KL | Yageo | 311-10.0KHRCT-ND |  |  | Cut Tape (CT) | Active | 1 | 0.10000 | $0.10 | 11537391 | 24 Weeks | RES SMD 10K OHM 1% 1/10W 0603 | ROHS3 Compliant | Lead free | REACH Unaffected

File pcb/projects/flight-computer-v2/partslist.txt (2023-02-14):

Partlist exported from /var/folders/g1/yrlxd1nn5657qgv2xyx0zvf00000gn/T/Neutron/ElectronFileOutput/82780/sch-aead1a05-c479-4852-bf5b-3867639da8be/flight-computer v6.sch at 2/14/23 9:53 AM

Part Value                           Device                          Package                              Description                                                                                  CATEGORY  DESCRIPTION                                                                                                         DIGI-KEY_PART_NUMBER  DIGI-KEY_PURCHASE_URL                                                                                                                                      MANUFACTURER MF                     MP                 MPN OPERATING_TEMP PACKAGE                     PART_STATUS POPULARITY PURCHASE-URL                                                        ROHS_COMPLIANT SERIES SPICEPREFIX SUB-CATEGORY THERMALLOSS TYPE
C1   0.1uF                           C-EUC0603                       C0603                                CAPACITOR, European symbol                                                                                                                                                                                                                                                                                                                                                                                                                                                                                                    73                                                                                                   C                                        
C2   0.1uF                           C-EUC0603                       C0603                                CAPACITOR, European symbol                                                                                                                                                                                                                                                                                                                                                                                                                                                                                                    73                                                                                                   C                                        
C3   0.1uF                           C-EUC0603                       C0603                                CAPACITOR, European symbol                                                                                                                                                                                                                                                                                                                                                                                                                                                                                                    73                                                                                                   C                                        
C6   0.1uF                           C-EUC0603                       C0603                                CAPACITOR, European symbol                                                                                                                                                                                                                                                                                                                                                                                                                                                                                                    73                                                                                                   C                                        
C7   0.1uF                           C-EUC0603                       C0603                                CAPACITOR, European symbol                                                                                                                                                                                                                                                                                                                                                                                                                                                                                                    73                                                                                                   C                                        
C8   0.1uF                           C-EUC0603                       C0603                                CAPACITOR, European symbol                                                                                                                                                                                                                                                                                                                                                                                                                                                                                                    73                                                                                                   C                                        
C9   0.1uF                           C-EUC0603                       C0603                                CAPACITOR, European symbol                                                                                                                                                                                                                                                                                                                                                                                                                                                                                                    73                                                                                                   C                                        
C10  0.1uF                           C-EUC0603                       C0603                                CAPACITOR, European symbol                                                                                                                                                                                                                                                                                                                                                                                                                                                                                                    73                                                                                                   C                                        
C11  0.1uF                           C-EUC0603                       C0603                                CAPACITOR, European symbol                                                                                                                                                                                                                                                                                                                                                                                                                                                                                                    73                                                                                                   C                                        
C12  0.1uF                           C-EUC0603                       C0603                                CAPACITOR, European symbol                                                                                                                                                                                                                                                                                                                                                                                                                                                                                                    73                                                                                                   C                                        
C13  0.1uF                           C-EUC0603                       C0603                                CAPACITOR, European symbol                                                                                                                                                                                                                                                                                                                                                                                                                                                                                                    73                                                                                                   C                                        
C14  0.1uF                           C-EUC0603                       C0603                                CAPACITOR, European symbol                                                                                                                                                                                                                                                                                                                                                                                                                                                                                                    73                                                                                                   C                                        
C15  0.1uF                           C-EUC0603                       C0603                                CAPACITOR, European symbol                                                                                                                                                                                                                                                                                                                                                                                                                                                                                                    73                                                                                                   C                                        
C17  0.1uF                           C-EUC0603                       C0603                                CAPACITOR, European symbol                                                                                                                                                                                                                                                                                                                                                                                                                                                                                                    73                                                                                                   C                                        
C18  0.1uF                           C-EUC0603                       C0603                                CAPACITOR, European symbol                                                                                                                                                                                                                                                                                                                                                                                                                                                                                                    73                                                                                                   C                                        
C19  0.1uF                           C-EUC0603                       C0603                                CAPACITOR, European symbol                                                                                                                                                                                                                                                                                                                                                                                                                                                                                                    73                                                                                                   C                                        
C20  0.1uF                           C-EUC0603                       C0603                                CAPACITOR, European symbol                                                                                                                                                                                                                                                                                                                                                                                                                                                                                                    73                                                                                                   C                                        
C22  10µF                            CAP_CERAMIC0805-NOOUTLINE       0805-NO                              Ceramic Capacitors                                                                                                                                                                                                                                                                                                                                                                                                                                                                                                                                                                                                                                                          
C23  0.1uF                           C-EUC0603                       C0603                                CAPACITOR, European symbol                                                                                                                                                                                                                                                                                                                                                                                                                                                                                                    73                                                                                                   C                                        
C24  0.1uF                           C-EUC0603                       C0603                                CAPACITOR, European symbol                                                                                                                                                                                                                                                                                                                                                                                                                                                                                                    73                                                                                                   C                                        
C25  0.1uF                           C-EUC0603                       C0603                                CAPACITOR, European symbol                                                                                                                                                                                                                                                                                                                                                                                                                                                                                                    73                                                                                                   C                                        
C26  0.1uF                           C-EUC0603                       C0603                                CAPACITOR, European symbol                                                                                                                                                                                                                                                                                                                                                                                                                                                                                                    73                                                                                                   C                                        
C27  0.1uF                           C-EUC0603                       C0603                                CAPACITOR, European symbol                                                                                                                                                                                                                                                                                                                                                                                                                                                                                                    73                                                                                                   C                                        
C28  0.1uF                           C-EUC0603                       C0603                                CAPACITOR, European symbol                                                                                                                                                                                                                                                                                                                                                                                                                                                                                                    73                                                                                                   C                                        
C29  1uF                             CAP_CERAMIC0603_NO              0603-NO                              Ceramic Capacitors                                                                                                                                                                                                                                                                                                                                                                                                                                                                                                                                                                                                                                                          
C30  10µF                            CAP_CERAMIC0805-NOOUTLINE       0805-NO                              Ceramic Capacitors                                                                                                                                                                                                                                                                                                                                                                                                                                                                                                                                                                                                                                                          
H1   MOUNT-PAD-ROUND2.8              MOUNT-PAD-ROUND2.8              2,8-PAD                              MOUNTING PAD, round                                                                                                                                                                                                                                                                                                                                                                                                                                                                                                           6                                                                                                                                             
H2   MOUNT-PAD-ROUND2.8              MOUNT-PAD-ROUND2.8              2,8-PAD                              MOUNTING PAD, round                                                                                                                                                                                                                                                                                                                                                                                                                                                                                                           6                                                                                                                                             
H3   MOUNT-PAD-ROUND2.8              MOUNT-PAD-ROUND2.8              2,8-PAD                              MOUNTING PAD, round                                                                                                                                                                                                                                                                                                                                                                                                                                                                                                           6                                                                                                                                             
H4   MOUNT-PAD-ROUND2.8              MOUNT-PAD-ROUND2.8              2,8-PAD                              MOUNTING PAD, round                                                                                                                                                                                                                                                                                                                                                                                                                                                                                                           6                                                                                                                                             
H5   MOUNT-PAD-ROUND2.8              MOUNT-PAD-ROUND2.8              2,8-PAD                              MOUNTING PAD, round                                                                                                                                                                                                                                                                                                                                                                                                                                                                                                           6                                                                                                                                             
H6   MOUNT-PAD-ROUND2.8              MOUNT-PAD-ROUND2.8              2,8-PAD                              MOUNTING PAD, round                                                                                                                                                                                                                                                                                                                                                                                                                                                                                                           6                                                                                                                                             
H7   MOUNT-PAD-ROUND2.8              MOUNT-PAD-ROUND2.8              2,8-PAD                              MOUNTING PAD, round                                                                                                                                                                                                                                                                                                                                                                                                                                                                                                           6                                                                                                                                             
H8   MOUNT-PAD-ROUND2.8              MOUNT-PAD-ROUND2.8              2,8-PAD                              MOUNTING PAD, round                                                                                                                                                                                                                                                                                                                                                                                                                                                                                                           6                                                                                                                                             
H9   MOUNT-PAD-ROUND2.8              MOUNT-PAD-ROUND2.8              2,8-PAD                              MOUNTING PAD, round                                                                                                                                                                                                                                                                                                                                                                                                                                                                                                           6                                                                                                                                             
H10  MOUNT-PAD-ROUND2.8              MOUNT-PAD-ROUND2.8              2,8-PAD                              MOUNTING PAD, round                                                                                                                                                                                                                                                                                                                                                                                                                                                                                                           6
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

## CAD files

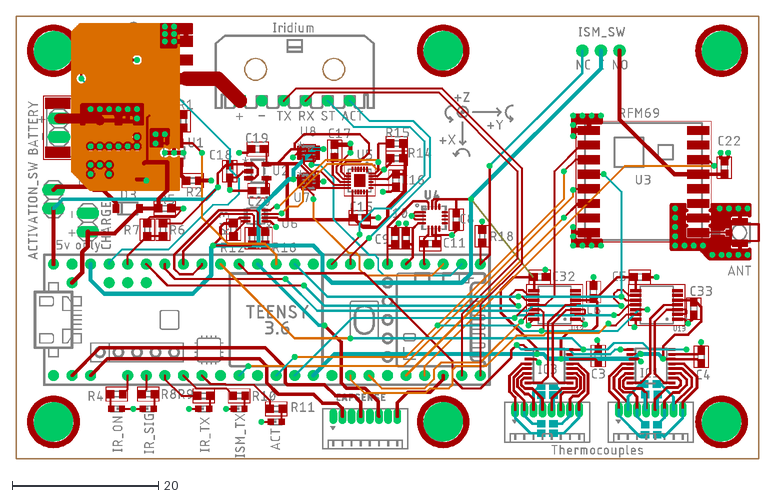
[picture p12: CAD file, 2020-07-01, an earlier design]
pcb/projects/flight-computer/flight-computer.dxf
101.7 x 60.6

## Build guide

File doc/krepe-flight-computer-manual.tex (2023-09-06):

\documentclass{article}
\usepackage[utf8]{inputenc}

\title{KREPE-2 Avionics Documentation}
\author{Matt Ruffner}
\date{}

\usepackage{url}
\usepackage{float}
\usepackage{tikz}
\usepackage{natbib}
\usepackage{graphicx}
\usepackage{listings}
\usepackage{fullpage}
\usepackage{hyperref}
\hypersetup{
    colorlinks=true,
    linkcolor=blue,
    filecolor=magenta,      
    urlcolor=cyan,
}

\begin{document}

\maketitle
\tableofcontents
\listoffigures
\listoftables
\newpage

%%%%%%%%%%%%%%%%%%%%%%%%%%%%%%%%%%%%%%%%%%%%%%%%%%%%%%%%%%%%%%%%%%%%%%%%%%%%%%%%%%%%%%%%%
%%%%%%%%%%%%%%%%%%%%%%%%%%%%%%%%%%%%%%%%%%%%%%%%%%%%%%%%%%%%%%%%%%%%%%%%%%%%%%%%%%%%%%%%%
%%%%%%%%%%%%%%%%%%%%%%%%%%%%%%%%%%%%%%%%%%%%%%%%%%%%%%%%%%%%%%%%%%%%%%%%%%%%%%%%%%%%%%%%%
%%%%%%%%%%%%%%%%%%%%%%%%%%%%%%%%%%%%%%%%%%%%%%%%%%%%%%%%%%%%%%%%%%%%%%%%%%%%%%%%%%%%%%%%%
\section{Introduction}

This document contains information about the flight computer for the KREPE-2 mission as well as the safety precautions taken to ensure the flight hardware is not a danger to the ISS or its astronauts. In addition to electrical designs and schematics, this document contains pin names, links to datasheets, and implementation notes. The following sections outline the subsystems of the flight computer and pin names for software usage. Other details about the power subsystem including battery type and rating are also included. 

There are a total of 5 capsules in the KREPE-2 mission, an increase from the 3 capsules present in the original KREPE mission (now referred to as KREPE-1). The table below shows the part names and numbers of the 5 capsules as presented to NASA for integration with a resupply mission.

\begin{table}[H]
\centering
\caption{Part names and numbers for the KREPE-2 capsules.}
\label{tab:partnames}
\begin{tabular}{l | l}
Part Name & Part Number \\
\hline
KREPE-2-SPICA & KREPE-2-001 \\
KREPE-2-CPICA & KREPE-2-003 \\
KREPE-2-AMTPS & KREPE-2-002 \\
KREPE-2-REUSE & KREPE-2-004 \\
KREPE-2-FFORM & KREPE-2-004 \\
\end{tabular}
\end{table}

The entire flight ready assembly is referred to as KREPE, which consists of a capsule containing the science (flight computer, batteries, etc.) and a metal shell known as KREM that acts as a Faraday cage, inhibiting any inadvertent RF radiation from the capsule. Both primary and secondary activation must occur for the capsule to become fully active and begin RF transmissions. To avoid accidental activation of hazardous subsystems, secondary activation criteria must be met. Primary and secondary activation processes are discussed in sections ~\ref{sec:primary-activation},\ref{sec:secondary-activation}, and \ref{sec:radio-power-control}.

The subsystems of the flight computer are outlined in Sec.~\ref{sec:subsystems}. Pin definitions are listed with each hardware or sensor component along with any relevant information regarding safety or implementation. Electrical schematics, microcontroller reference cards, and a partslist are shown in  Appendices ~\ref{appa}, \ref{app:pinmap}, and \ref{app:partslist}, respectively.

\subsection{Primary Activation}
\label{sec:primary-activation}

%\begin{tikzpicture}[
%   every node/.append style={circle, draw=blue!80, inner sep=0pt, minimum size=12pt}]
%\node                 (1) at (0,0) {1};
%\node[thick]          (2) at (1,0) {2};
%\node[draw=white,text=black] (...) at (2,0) {...};
%\end{tikzpicture}

Primary activation is triggered by a pin pulled out of KREPE by astronauts. Once the pin is pulled, a mechanical switch\footnote{\url{https://www.digikey.com/en/products/detail/panasonic-electric-works/ABJ362860/4691828}} is closed and the flight computer boots to dormant mode where it consumes minimal power. The Iridium radio is not powered on in dormant mode. After pulling the pull tab, an astronaut places a piece of copper tape over the hole, resealing the faraday cage effect of the KREM, and primary activation is the complete. Copper tape ensures the KREM is completely sealed with regard to inadvertent EMI while on station.

A schematic showing battery protection and primary activation circuitry activation is shown in Fig. \ref{fig:activation-circuitry}. Less than 5 inches of copper 20 AWG PVC insulated wire is used to connect the batteries to the first power function (battery protection circuitry).

%The \texttt{POWER\_SW} header must closed for protected battery or USB voltage to be applied to the Teensy's VIN pin, powering on the system. The location of these connection points can be seen in Fig. \ref{fig:board-top} labelled on the silk screen in the left middle of the PCB. A rendering of the bottom of the board is shown in Fig. \ref{fig:board-bottom}.

\begin{figure}[H]
    \centering
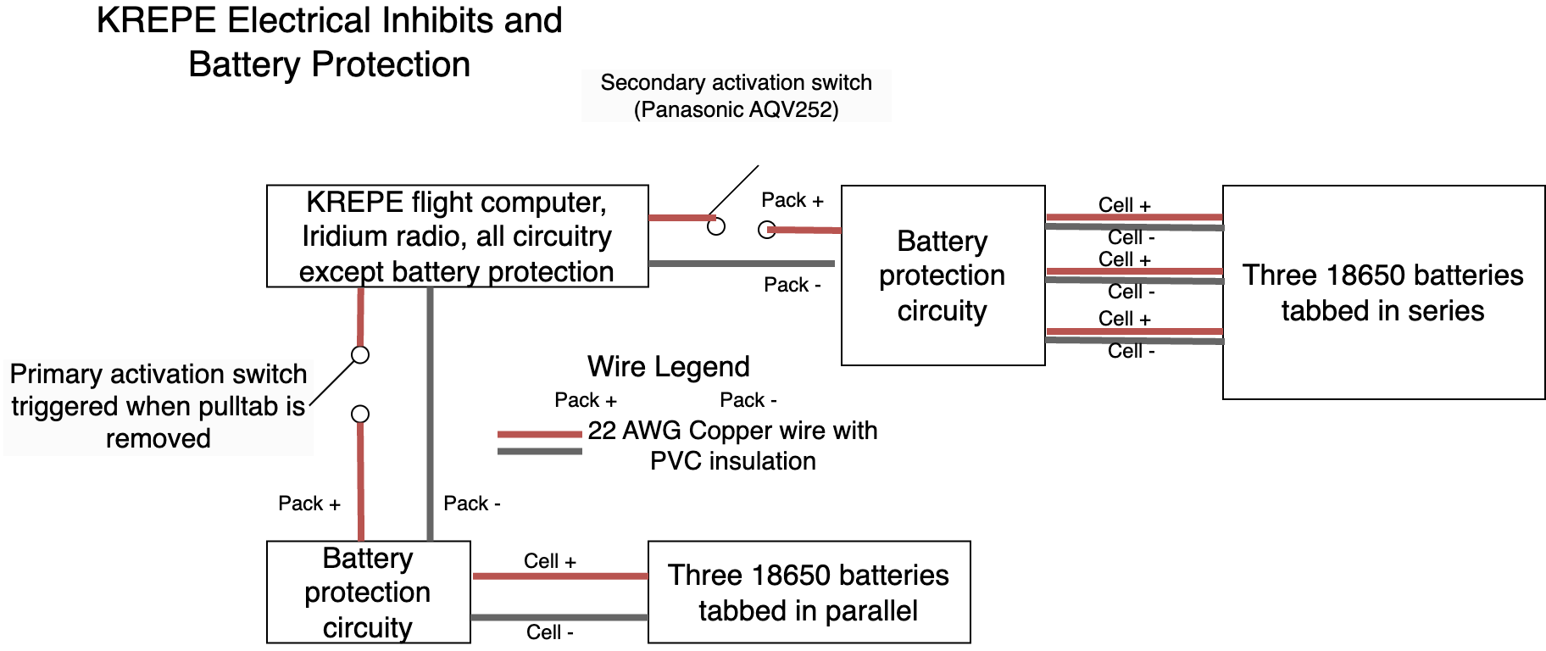
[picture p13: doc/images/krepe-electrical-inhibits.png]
    
    \caption{Activation and battery protection schematic overview.}
    \label{fig:activation-circuitry}
\end{figure}

%There is an low power 915MHz ISM band debug communication link that is only used during testing on the ground and is physically disconnected from power before once handed over for final integration. The \texttt{ISM\_SW} header is meant to enable and disable the RFM69 debug radio. The center 3.3V pin of this header is connected to the normally closed labeled pin, a GPIO pin is pulled high (see Fig. \ref{tab:pins_radio}). When the normally closed pin is connected to the center pin, the RFM69 is enabled. 

\subsection{Secondary Activation}
\label{sec:secondary-activation}
Once primary activation is complete and the flight computer is in dormant mode, a digital input to the flight computer is configured as an interrupt to sense when the KREM separates from around the capsule. This secondary activation interrupt is triggered during re-entry when the KREM heats to a temperature that is sufficient to melt the polycarbonate bolts that hold it together. No radio transmissions are attempted before secondary activation. The Iridium radio remains unpowered until secondary activation, when flight software turns on the Panasonic AQV252 digital switch, powering up the  communications and sensor electronics.

%%%%%%%%%%%%%%%%%%%%%%%%%%%%%%%%%%%%%%%%%%%%%%%%%%%%%%%%%%%%%%%%%%%%%%%%%%%%%%%%%%%%%%%%%
%%%%%%%%%%%%%%%%%%%%%%%%%%%%%%%%%%%%%%%%%%%%%%%%%%%%%%%%%%%%%%%%%%%%%%%%%%%%%%%%%%%%%%%%%
%%%%%%%%%%%%%%%%%%%%%%%%%%%%%%%%%%%%%%%%%%%%%%%%%%%%%%%%%%%%%%%%%%%%%%%%%%%%%%%%%%%%%%%%%
%%%%%%%%%%%%%%%%%%%%%%%%%%%%%%%%%%%%%%%%%%%%%%%%%%%%%%%%%%%%%%%%%%%%%%%%%%%%%%%%%%%%%%%%%
%%%%%%%%%%%%%%%%%%%%%%%%%%%%%%%%%%%%%%%%%%%%%%%%%%%%%%%%%%%%%%%%%%%%%%%%%%%%%%%%%%%%%%%%%
%%%%%%%%%%%%%%%%%%%%%%%%%%%%%%%%%%%%%%%%%%%%%%%%%%%%%%%%%%%%%%%%%%%%%%%%%%%%%%%%%%%%%%%%%
%%%%%%%%%%%%%%%%%%%%%%%%%%%%%%%%%%%%%%%%%%%%%%%%%%%%%%%%%%%%%%%%%%%%%%%%%%%%%%%%%%%%%%%%%
%%%%%%%%%%%%%%%%%%%%%%%%%%%%%%%%%%%%%%%%%%%%%%%%%%%%%%%%%%%%%%%%%%%%%%%%%%%%%%%%%%%%%%%%%
\section{Subsystem Design}
\label{sec:subsystems}

The following sections outline the different sensor systems that are present on the KREPE-2 capsules, including their placement along the forebody and relative position to other sensors. An overview of the hardware and sensors that are in a KREPE capsule, along with the electrical connections to the flight computer are shown in Fig. \ref{fig:hardware-diagram}.

\begin{figure}[H]
    \centering
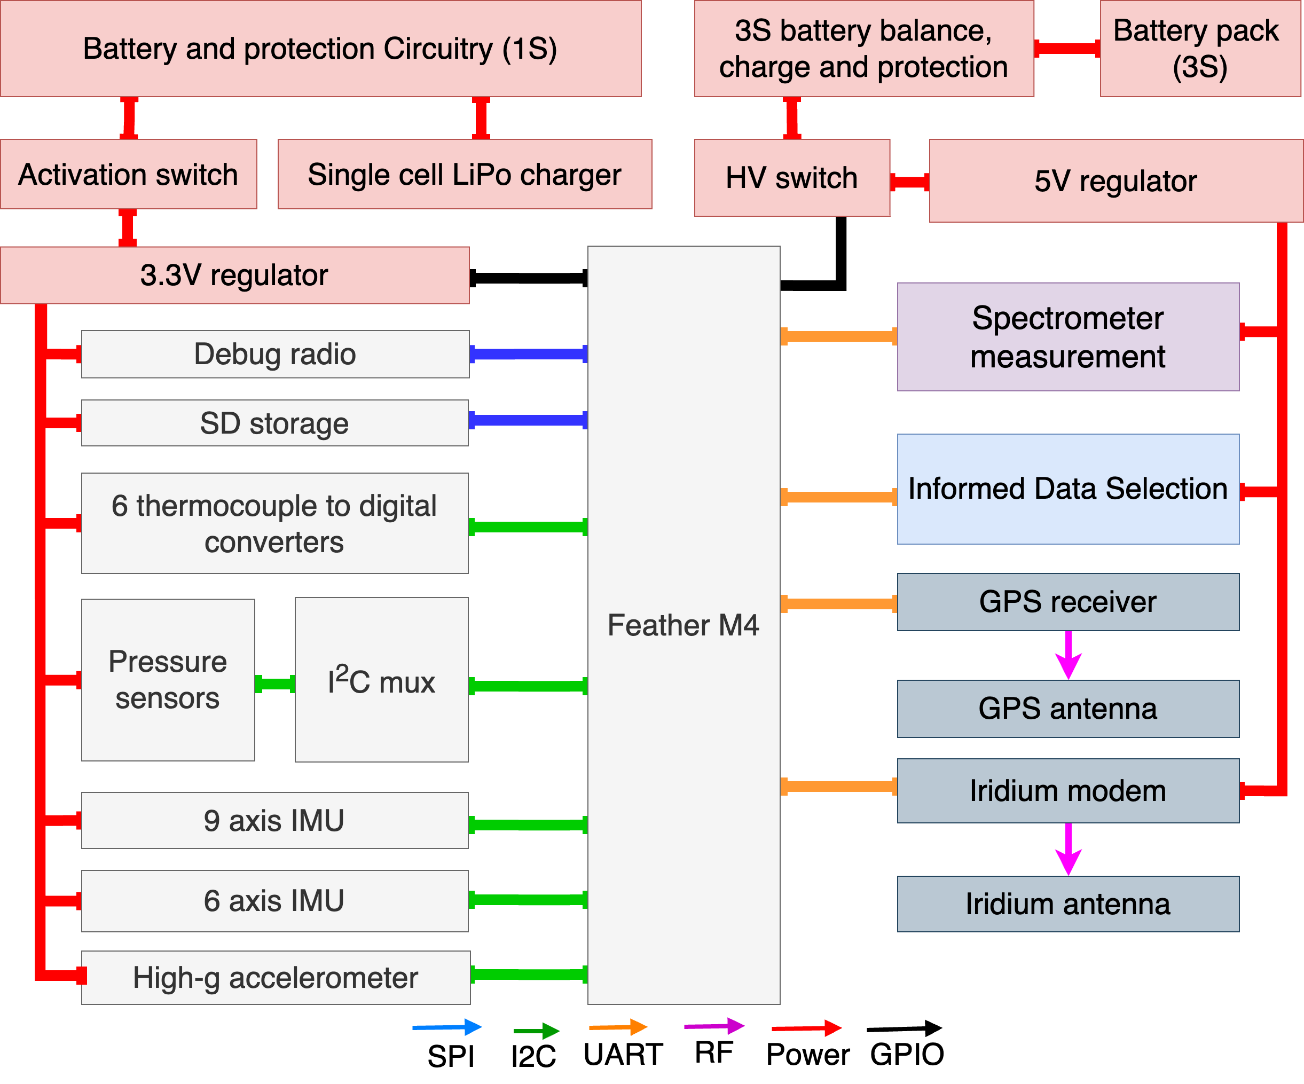
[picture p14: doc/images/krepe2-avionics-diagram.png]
    
    \caption{Overview of the KRUPS flight computer and subsystem connections.}
    \label{fig:hardware-diagram}
\end{figure}

\subsection{Thermal Measurement}
The thermal measurement subsystem is used to take readings from up to six thermocouples (TCs) embedded within the TPS surrounding each capsule.  The locations for the thermal measurement points with respect to the internal housing are shown in Fig. \ref{fig:sensor-locations}, along with other sensor locations such as ported pressure sensors and spectrometers.

\begin{figure}
\centering
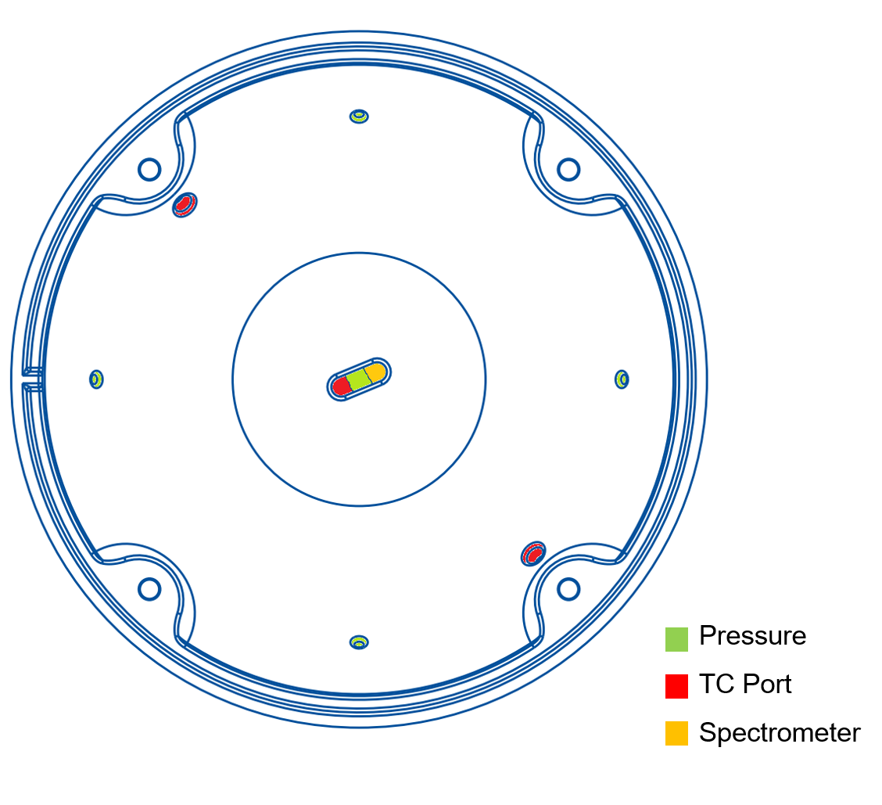
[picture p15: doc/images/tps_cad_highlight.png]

\label{fig:sensor-locations}
\caption{Thermal, pressure, and spectral measurement location on the capsule forebody.}
\end{figure}

The thermocouple to digital conversion system on KREPE-2 uses 6 MCP-9600 TC to digital converters linked via I2C bus. This is an improvement over the multiplexed converter setup used in the first KREPE mission. A low pass filter is included between the TC connector points and each MCP-9600 to help suppress spurious measurements.
%%
%\begin{figure}[H]
%  \centering
%    \includegraphics[width=0.5\textwidth]{images/krepe2-tc-closeup}
 %   \caption{TC connection points for three of the six TC to digital conversion chips on the KREPE- flight computer. The plated holes accept solderable threaded inserts which make connecting TC lead wires much easier compare to the KREPE-1 flight computer, which required TC leads to be crimped into a Molex PicoBlade connector.}
%    \label{fig:tc-closeup}
%\end{figure}

%%%%%%%%%%%%%%%%%%%%%%%%%%%%%%%%%%%%%%%%%%%%%%%%
\subsection{Pressure Measurement}
The KREPE-2 capsule design includes an array of ported pressure sensors in a cross configuration, constitutes what is known as a flushed air data sensing (FADS) system. Such FADS systems are very useful in the reconstruction of the re-entry trajectory attitude\cite{TODO}. Flexible PTFE tubing is used  to connect the hole in the forebody to the barb on the pressure sensor. An image of the Honeywell sensor used is shown in Fig. \ref{fig:pressure-sensor}.

\begin{figure}[H]
\centering
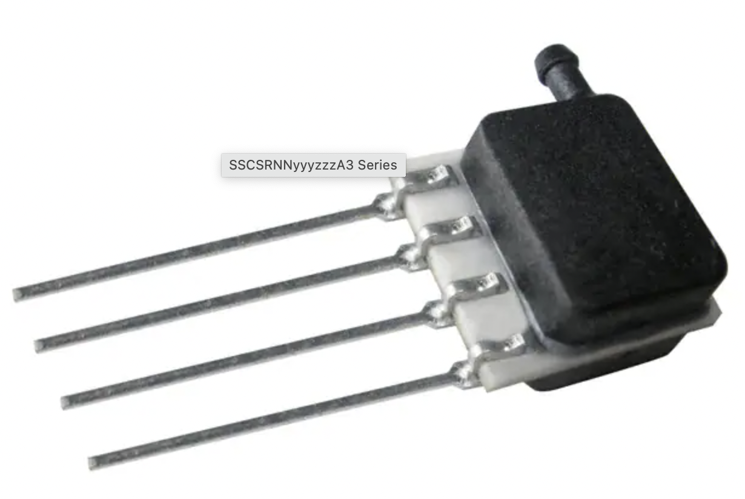
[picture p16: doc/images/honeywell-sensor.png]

\caption{Honeywell ported pressure sensor used for the FADS system. }
\label{fig:pressure-sensor}
\end{figure}

%%%%%%%%%%%%%%%%%%%%%%%%%%%%%%%%%%%%%%%%%%%%%%%%%%%%%%%%%%%%%
\subsection{Spectrometer Subsystem}
Another addition to the sensor suite on the KREPE-2 capsules is a Hamamatsu C12880 miniature spectrometer\footnote{\url{https://www.hamamatsu.com/content/dam/hamamatsu-photonics/sites/documents/99_SALES_LIBRARY/ssd/c12880ma_kacc1226e.pdf}}.

Due to the position that the spectrometer must be in, in the nose (stagnation point) of the capsule, there is a need for a processing element in the same region. For this reason we are working on implementing a Battery and Spectrometer Measurement System (BSMS). This BSMS will be able to read the spectrometer as well as monitor the system battery voltages. 

%%%%%%%%%%%%%%%%%%%%%%%%%%%%%%%%%%%%%%%%%%%%%%%%%%%%%%%%%%%%%
\subsection{Inertial Measurement}
The KREPE-2 flight computer also features multiple inertial measurement sensors to collect rotational rates and accelerations experienced by the capsule during re-entry. Like FADS measurements, the IMU data collected by the capsule will also greatly aid the post-flight reconstruction of the re-entry environment which occurred for each capsule.

The inertial sensors present on the KREPE-2 flight computer are an FSM300, ICM-42670, and an H3LIS100. The FSM300 is a preassembled unit which features a BNO-088 9 axis IMU. The maximum acceleration measurable by the FSM300 is $\pm$16g. The ICM-42670 is an additional 6-axis IMU included as an evaluation platform. The primary IMU is the FSM300. The H3LIS100 is a 3-axis accelerometer, included for measuring accelerations on the capsule which are greater than $\pm$16g.

%\paragraph{Barometric Pressure Sensor}
%Version 1.1 of the flight computer features an Infineon DSP310 barometric pressure and temperature sensor connected to the SPI bus with active low chip select on pin 8 of the Teensy. This sensor is not used for activation detection. 

%%%%%%%%%%%%%%%%%%%%%%%%%%%%%%%%%%%%%%%%%%%%%%%%%%%%%%%%%%%%%%%55
\subsection{Power and Batteries}

The power and battery subsystem on the KREPE-2 capsules has improved features and capacity from the KREPE-1 design. Batteries are still provided by NASA Cargo Mission Contract (CMC) fulfilled by JSC and rated at 3200mAh each. KREPE-2 features two separate battery packs which allow for greater flexibility when designing any future capsule instrumentation. Three cells are tabbed in series to provide a 3S1P pack (11.1V nominal), as well as a secondary system pack which consists of 3 cells tabbed in parallel, or 1S3P. %The 1S3P (3.7V nominal) pack is an improvement over the 1S2P pack of KREPE-1 which powered the entire system.

The 3.7V pack powers the flight computer, but not any high-draw peripherals (GPS, Iridium modem, spectrometer, etc). The 11.1V pack is switched on after secondary activation and powers any high draw peripherals through an optional 5V buck regulator. 

Battery classification, product, and model number can be seen in Fig. \ref{fig:bat-spec} (taken from battery specification sheet).

\begin{figure}[h!]
	\centering
	
	\label{fig:bat-spec}
	\caption{Sanyo battery specifications from the datasheet.}
\end{figure}

The 3.7 pack is able to be recharged through the MCP73831\footnote{ (\url{https://www.microchip.com/wwwproducts/en/MCP73831})} present on the Feather M4, however the 11.1V pack currently be charged externally through a separate balance connector which does not connect to the flight computer.  

There is work ongoing which aims to support the monitoring of the 3S1P pack. This system will also interface with the spectrometer. 

Charging is only performed on the ground and there is no provision for charging in flight. Schematics and electrical connections are shown in Fig. \ref{fig:page1-3} in Appendix \ref{appa}.

%\subsubsection{Battery Status Interface}
%Throught BSMS...

\subsubsection{Battery Protection}
Protection circuitry is implemented on each of the two battery packs present on the KREPE-2 capsules. 

 We are using a DW01-P Voltage and Current Protection IC for the 3.7V and 11.1V system packs  \footnote{\url{https://cdn.sparkfun.com/assets/learn_tutorials/2/5/1/DW01-P_DataSheet_V10.pdf}}.

The 11.1V auxiliary pack has a separate battery protection circuit that protects it from over current, under voltage, and over voltage conditions.

\begin{figure}[H]
	\centering
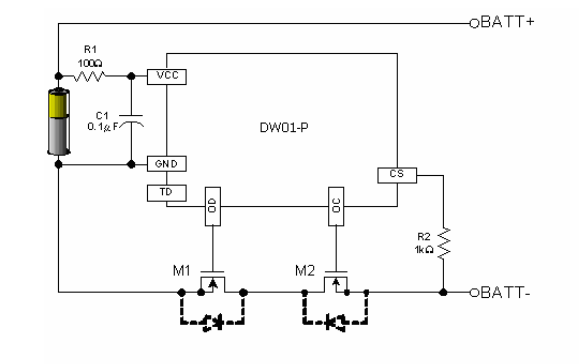
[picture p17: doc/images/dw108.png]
	
	\caption{Battery protection circuitry.}
	\label{fig:bat-protec}
\end{figure}

Protection circuitry as implemented on the KREPE flight computer PCB is shown in Fig. \ref{fig:bat-protec}. Our two battery packs are both connected to their respective battery protection circuitry, then  to primary activation switches. This protection circuitry is upstream of the primary activation switch. The battery protection PCB can be seen in Fig. \ref{fig:bat-protect}.

\begin{figure}[H]
	\centering
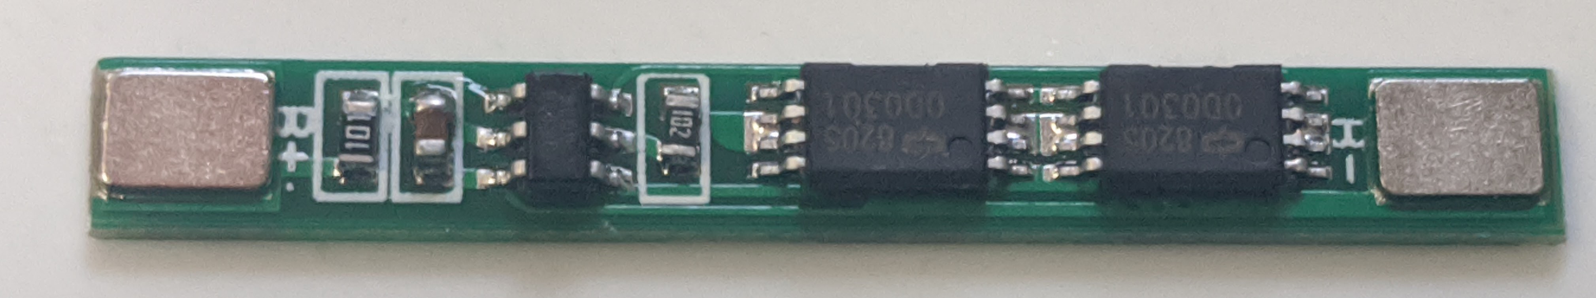
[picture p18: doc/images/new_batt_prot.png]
	
	\caption{Battery protection PCB.}
	\label{fig:bat-protect}
\end{figure}

\paragraph{Over-current protection}
Both the 3.7V and 11.1 V packs have their own battery protection circuity as the first power function after the batteries and before any cabling goes to the avionics or flight computer. Pictures of the protection PCBs and overcurrent tests proving their effectiveness are shown in the following figures.

\begin{figure}[H]
	\centering
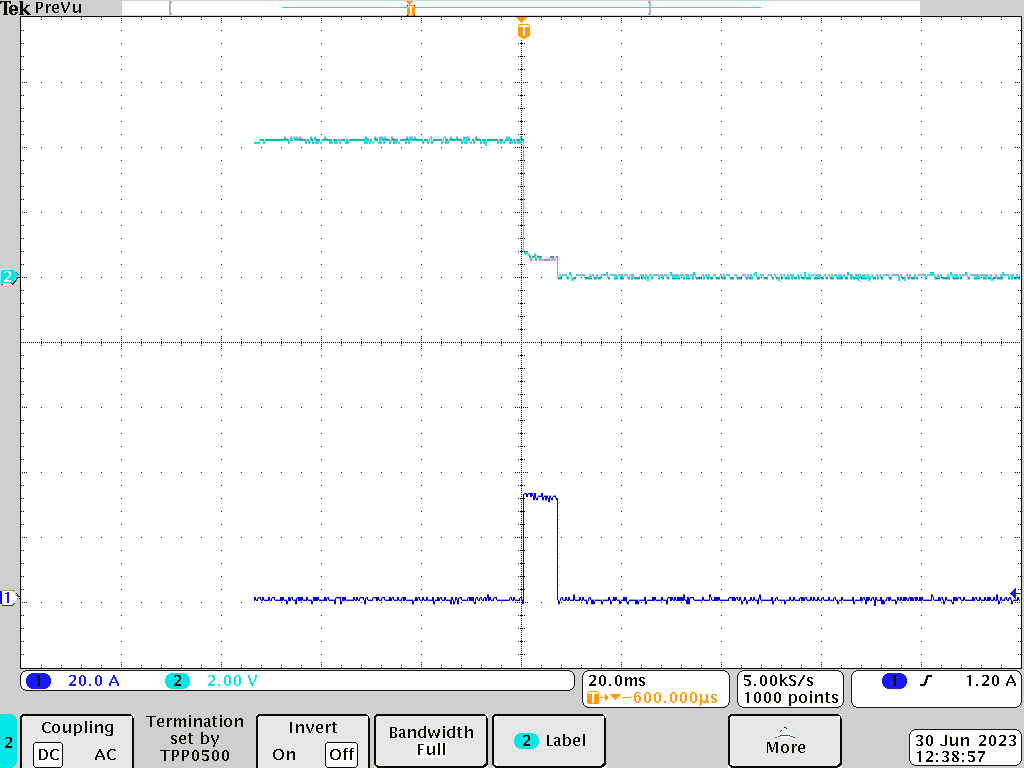
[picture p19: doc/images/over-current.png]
	
	\caption{The battery protection circuity disconnecting the cells after 6ms of over current condition. Blue: current. Purple: pack voltage.}
	\label{fig:over-current}
\end{figure}

The high voltage pack (3S) is protected by another PCB that also uses the DW01 protection IC, except it has three of these chips in the same circuit in order to protect a 3S (series) pack from overvoltage, undervoltage, and overcurrent conditions. An example of the 11.1V pack protection circuitry protecting from over current conditions can be seen in Fig. \ref{fig:3s-overcurrent}. The circuit protection board for the three cell series pack can be seen in Fig. \ref{fig:3s-protect}.

\begin{figure}
\centering
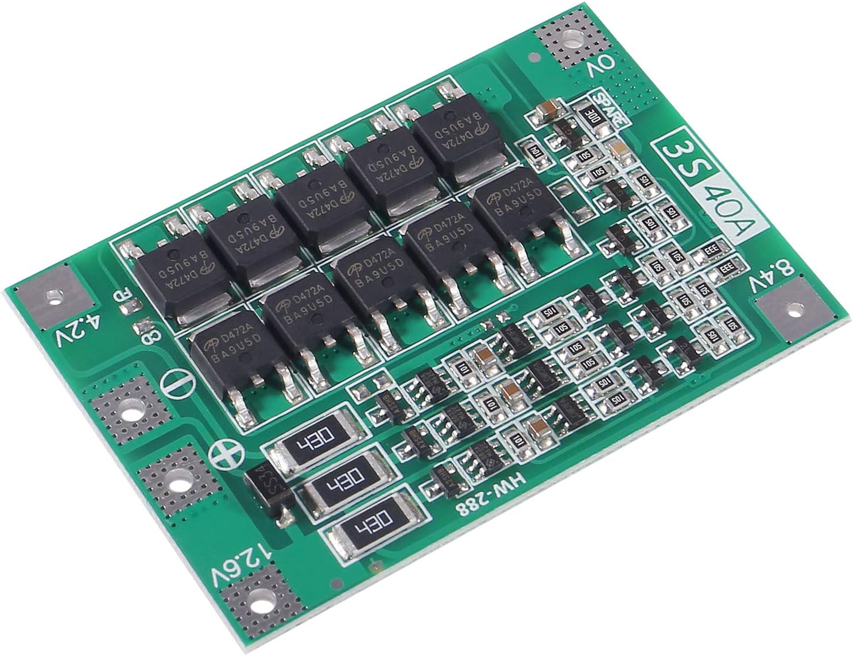
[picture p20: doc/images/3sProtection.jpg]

\caption{Battery protection board for the 3S 11.1 V pack.}
\label{fig:3s-protect}
\end{figure}

\begin{figure}
\centering
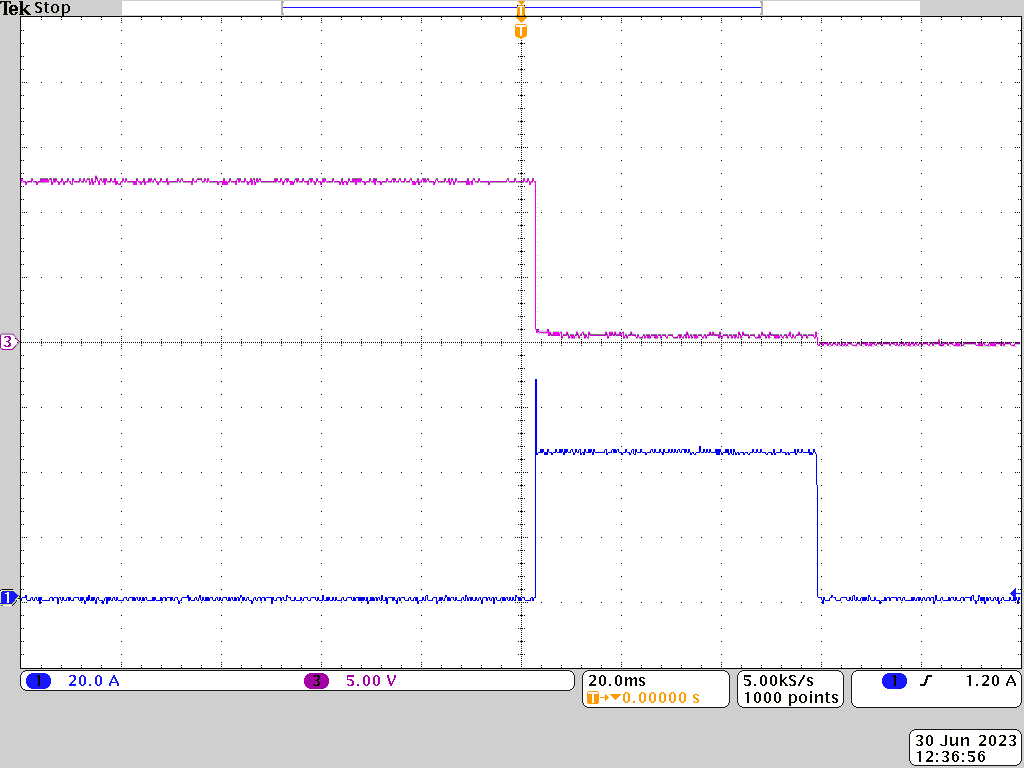
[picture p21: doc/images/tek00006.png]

\caption{Overcurrent protection test from 3S pack protection circuitry}
\label{fig:3s-overcurrent}
\end{figure}

%%%%%%%%%%%%%%%%%%%%%%%%%%%%%%%%%%%%%%%%%%%%%%%%%%%%%%%%%%%%%
\subsection{Visual Status Indicators}
There are individual LEDs on the POL switches connected to each serial port header, in addition to an indicator on the external 3v3 regulator. In addition to these indicators, the Feather M4 board also has an RGB led that is used to indicate program state

\section{PCB Assembly and Programming}

\subsection{Component placement and board bringup}

\begin{figure}[H]
\centering
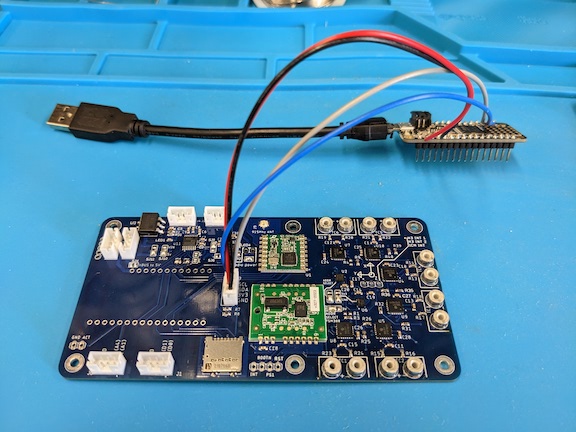
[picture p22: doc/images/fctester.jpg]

\caption{A freshly assembled flight computer with tester attached. The tester performs I$^2$C discovery and ensures all components are electrically connected}
\label{fig:fc-tester}
\end{figure}

\subsection{Solder Jumpers}

There are several solder jumpers on the KFC.
\begin{itemize}
\item \textbf{SJ8} selects which 3.3v source the RS232 translator chip will be powered from 
\item \textbf{SJ10} selects the voltage source for the optionally level shifted UART (designated for GPS) to be either 5V or VIN (the high voltage pack)
\item \textbf{SJ11} selects the voltage source for the level shifted UART (designated for the Iridium modem) to be either 5V or VIN ( the high voltage pack).
\end{itemize}

\subsection{Programming}

%%%%%%%%%%%%%%%%%%%%%%%%%%%%%%%%%%%%%%%%%%%%%%%%%%%%%%%%%%%%%%%%%%%%%%%%%%%%%%%%%%%
%%%%%%%%%%%%%%%%%%%%%%%%%%%%%%%%%%%%%%%%%%%%%%%%%%%%%%%%%%%%%%%%%%%%%%%%%%%%%%%%%%%
% APPENDIX
%%%%%%%%%%%%%%%%%%%%%%%%%%%%%%%%%%%%%%%%%%%%%%%%%%%%%%%%%%%%%%%%%%%%%%%%%%%%%%%%%%%
%%%%%%%%%%%%%%%%%%%%%%%%%%%%%%%%%%%%%%%%%%%%%%%%%%%%%%%%%%%%%%%%%%%%%%%%%%%%%%%%%%%
\appendix

\section{Schematics}
\label{appa}

\begin{figure}[H]
    \centering
    
    \caption{Page one of schematics.}
    \label{fig:page1-2}
\end{figure}

\begin{figure}[H]
    \centering
    
    \caption{Page two of schematics.}
    \label{fig:page1_1}
\end{figure}

\begin{figure}[H]
    \centering
    
    \caption{Page three of schematics.}
    \label{fig:page1-3}
\end{figure}

\begin{figure}[H]
    \centering
    
    \caption{Page four of schematics.}
    \label{fig:page1-4}
\end{figure}

%\begin{figure}[H]
%    \centering
%    \includegraphics[width=\textwidth]{images/page5.png}
%    \caption{Page five of schematics.}
%    \label{fig:page1-5}
%\end{figure}

\section{Board Renderings}
\begin{figure}[H]
	\centering
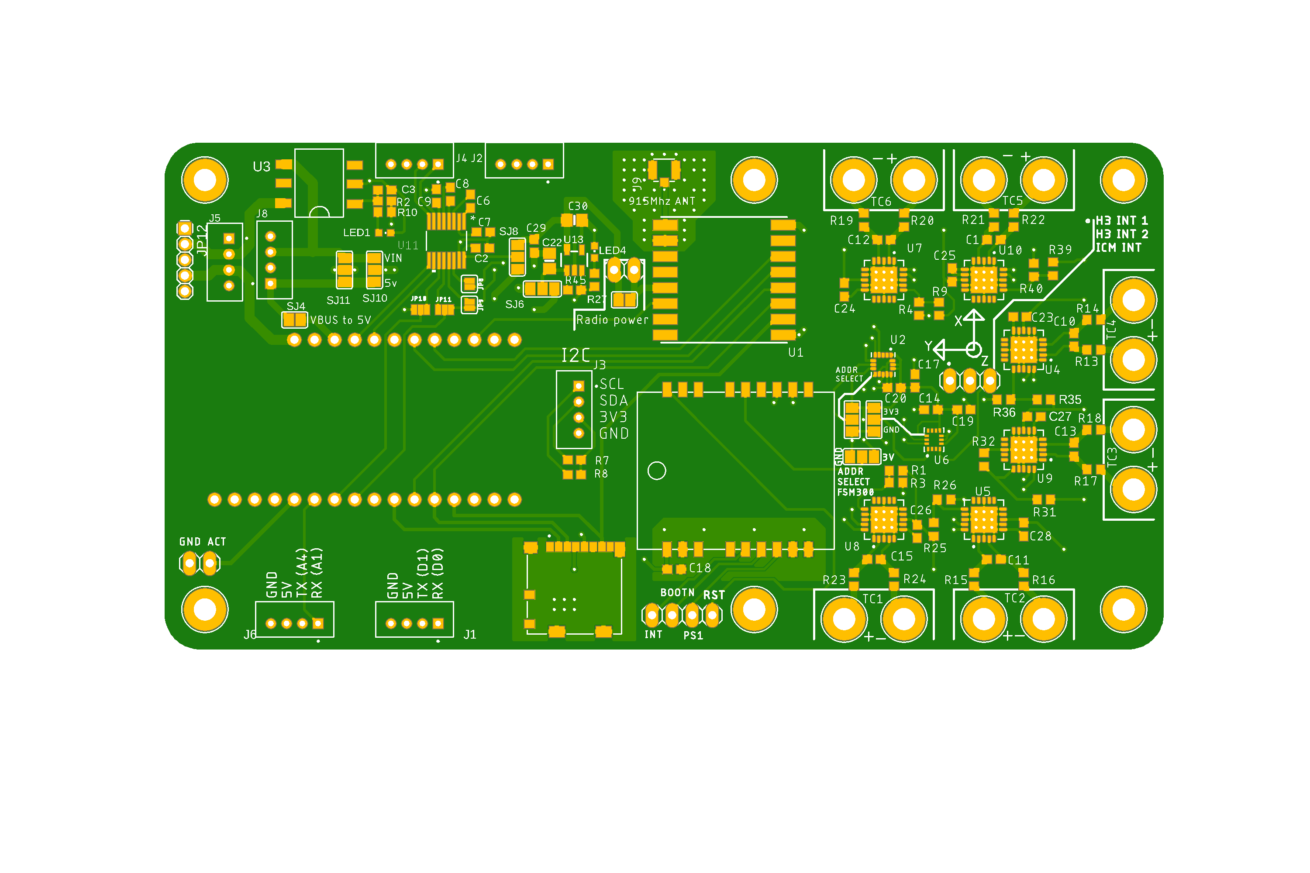
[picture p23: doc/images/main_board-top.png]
	
	\caption{Rendering of the top of the KREPE-2 control board.}
	\label{fig:board-top}
\end{figure}
\begin{figure}[H]
	\centering
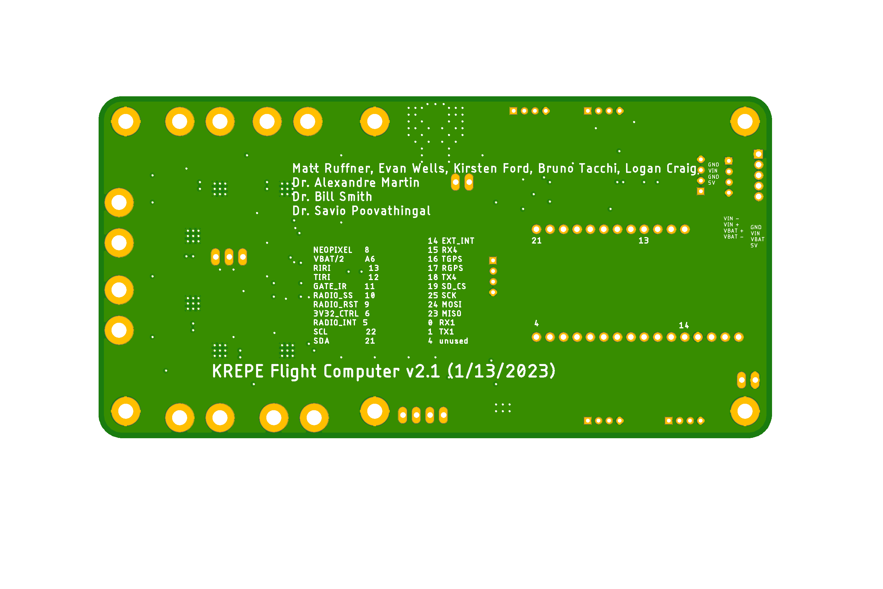
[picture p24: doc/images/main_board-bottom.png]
	
	\caption{Rendering of the bottom of the KREPE-2 control board.}
	\label{fig:board-bottom}
\end{figure}

%%%%%%%%%%%%%%%%%%%%%%%%
%%%%%%%%%%%%%%%%%%%%%%%%
\section{COTS hardware references}
This section contains reference cards for the COTS components used in the KREPE-2 capsules.
\subsection{Feather M4 Express}
\begin{figure}[H]
    \centering
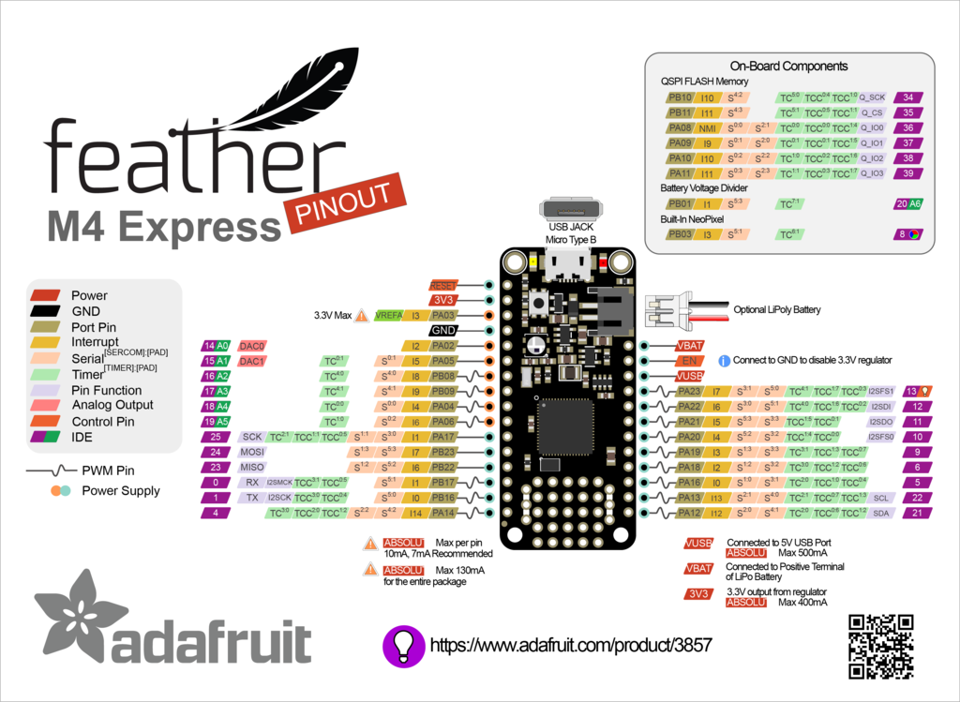
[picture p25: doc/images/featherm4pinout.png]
    
    \caption{Feather M4 Express}
    \label{fig:teensy-front}
\end{figure}

\subsection{Nano Pi Neo Air}
\begin{figure}[H]
    \centering
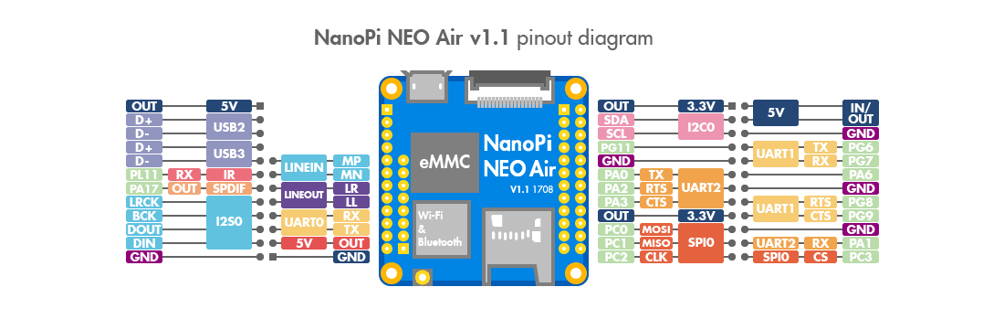
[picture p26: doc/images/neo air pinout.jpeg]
    
    \caption{NanoPi Neo Air reference sheet.}
    \label{fig:trinket-m0}
\end{figure}

\section{Partslist}
\label{app:partslist}
\lstinputlisting[language={},basicstyle=\tiny]{flight-computer-partslist.txt}

%%%%%%%%%%%%%%%%%%%%
%%%%%%%%%%%%%%%%%%%%
%%%%%%%%%%%%%%%%%%%%
% TODO: replace with FeatherM4 pin mapping
\newpage
\section{Arduino Pin Mapping}
\label{app:pinmap}
\lstinputlisting[language={}]{arduino-pinmap.txt}

%\bibliographystyle{plain}
%\bibliography{references}
\end{document}

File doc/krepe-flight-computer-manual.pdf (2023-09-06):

# KREPE-2 Avionics Documentation

Matt Ruffner

## Contents

1 Introduction | 3
1.1 Primary Activation | | 3
1.2 Secondary Activation | | 4
2 Subsystem Design | 4
2.1 Thermal Measurement | | 5
2.2 Pressure Measurement | | 6
2.3 Spectrometer Subsystem | | 6
2.4 Inertial Measurement | | 6
2.5 Power and Batteries | | 6
2.5.1 | Battery Protection | | 7
2.6 Visual Status Indicators | | 10
3 PCB Assembly and Programming | 10
3.1 Component placement and board bringup | | 10
3.2 Solder Jumpers | | 10
3.3 Programming | | 11
A Schematics | 11
B Board Renderings | 15
C COTS hardware references | 16
C.1 Feather M4 Express | | 17
C.2 Nano Pi Neo Air | | 17
D Partslist | 18
E Arduino Pin Mapping | 20

## List of Figures

1 | Activation and battery protection schematic overview | | 4
3 | Thermal, pressure, and spectral measurement location on the capsule forebody | | 5
2 | Overview of the KRUPS flight computer and subsystem connections | | 5
4 | Honeywell ported pressure sensor used for the FADS system | | 6
5 | Sanyo battery specifications from the datasheet | | 7
6 | Battery protection circuitry | | 7
7 | Battery protection PCB | | 8
8 | The battery protection circuity disconnecting the cells after 6ms of over current condition.
Blue: current. Purple: pack voltage | | 8

1

9 | Battery protection board for the 3S 11.1 V pack | | 9
10 | Overcurrent protection test from 3S pack protection circuitry | | 9
11 | A freshly assembled flight computer with tester attached. The tester performs I²C discovery
| and ensures all components are electrically connected | | 10
12 | Page one of schematics | | 11
13 | Page two of schematics | | 12
14 | Page three of schematics | | 13
15 | Page four of schematics | | 14
16 | Rendering of the top of the KREPE-2 control board | | 15
17 | Rendering of the bottom of the KREPE-2 control board | | 16
18 | Feather M4 Express | | 17
19 | NanoPi Neo Air reference sheet | | 17

## List of Tables

1 | Part names and numbers for the KREPE-2 capsules | | 3

2

## 1 Introduction

This document contains information about the flight computer for the KREPE-2 mission as well as the safety precautions taken to ensure the flight hardware is not a danger to the ISS or its astronauts. In addition to electrical designs and schematics, this document contains pin names, links to datasheets, and implementation notes. The following sections outline the subsystems of the flight computer and pin names for software usage. Other details about the power subsystem including battery type and rating are also included.
There are a total of 5 capsules in the KREPE-2 mission, an increase from the 3 capsules present in the original KREPE mission (now referred to as KREPE-1). The table below shows the part names and numbers of the 5 capsules as presented to NASA for integration with a resupply mission.

Table 1: Part names and numbers for the KREPE-2 capsules.
Part Name | Part Number
KREPE-2-SPICA | KREPE-2-001
KREPE-2-CPICA | KREPE-2-003
KREPE-2-AMTPS | KREPE-2-002
KREPE-2-REUSE | KREPE-2-004
KREPE-2-FFORM | KREPE-2-004

The entire flight ready assembly is referred to as KREPE, which consists of a capsule containing the science (flight computer, batteries, etc.) and a metal shell known as KREM that acts as a Faraday cage, inhibiting any inadvertent RF radiation from the capsule. Both primary and secondary activation must occur for the capsule to become fully active and begin RF transmissions. To avoid accidental activation of hazardous subsystems, secondary activation criteria must be met. Primary and secondary activation processes are discussed in sections 1.1,1.2, and ??.
The subsystems of the flight computer are outlined in Sec. 2. Pin definitions are listed with each hardware or sensor component along with any relevant information regarding safety or implementation. Electrical schematics, microcontroller reference cards, and a partslist are shown in Appendices A, E, and D, respec-tively.

### 1.1 Primary Activation

Primary activation is triggered by a pin pulled out of KREPE by astronauts. Once the pin is pulled, a mechanical switch¹
is closed and the flight computer boots to dormant mode where it consumes minimal power. The Iridium radio is not powered on in dormant mode. After pulling the pull tab, an astronaut places a piece of copper tape over the hole, resealing the faraday cage effect of the KREM, and primary activation is the complete. Copper tape ensures the KREM is completely sealed with regard to inadvertent EMI while on station.
A schematic showing battery protection and primary activation circuitry activation is shown in Fig. 1. Less than 5 inches of copper 20 AWG PVC insulated wire is used to connect the batteries to the first power function (battery protection circuitry).

1https://www.digikey.com/en/products/detail/panasonic-electric-works/ABJ362860/4691828

3

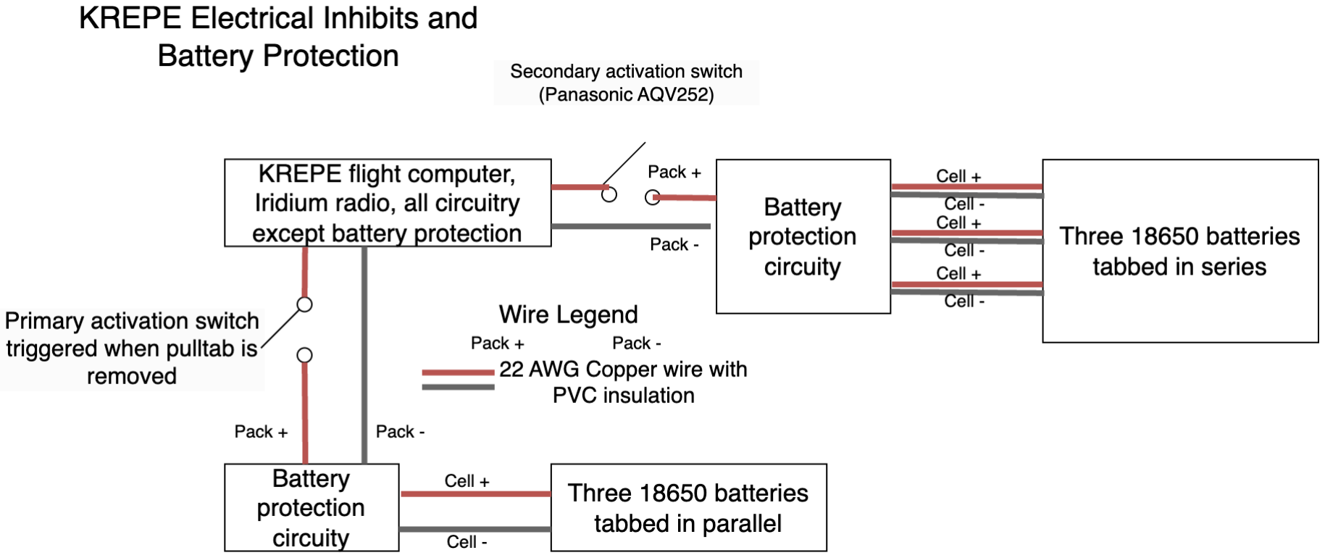
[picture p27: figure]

Figure 1: Activation and battery protection schematic overview.

### 1.2 Secondary Activation

Once primary activation is complete and the flight computer is in dormant mode, a digital input to the flight computer is configured as an interrupt to sense when the KREM separates from around the capsule. This secondary activation interrupt is triggered during re-entry when the KREM heats to a temperature that is sufficient to melt the polycarbonate bolts that hold it together. No radio transmissions are attempted before secondary activation. The Iridium radio remains unpowered until secondary activation.

## 2 Subsystem Design

The following sections outline the different sensor systems that are present on the KREPE-2 capsules, including their placement along the forebody and relative position to other sensors. An overview of the hardware and sensors that are in a KREPE capsule, along with the electrical connections to the flight computer are shown in Fig. 2.

4


Figure 3: Thermal, pressure, and spectral measurement location on the capsule forebody.

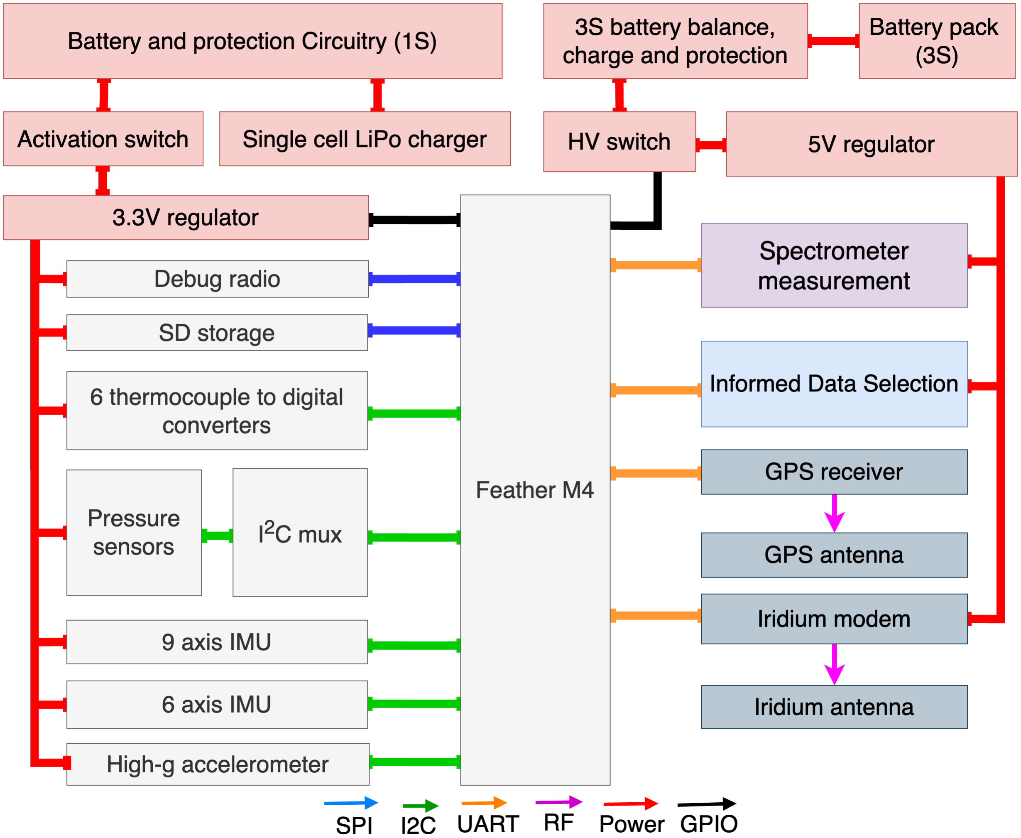
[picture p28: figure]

Figure 2: Overview of the KRUPS flight computer and subsystem connections.

### 2.1 Thermal Measurement

The thermal measurement subsystem is used to take readings from up to six thermocouples (TCs) embedded within the TPS surrounding each capsule. The locations for the thermal measurement points with respect to the internal housing are shown in Fig. 2.1, along with other sensor locations such as ported pressure sensors and spectrometers.
The thermocouple to digital conversion system on KREPE-2 uses 6 MCP-9600 TC to digital converters linked via I2C bus. This is an improvement over the multiplexed converter setup used in the first KREPE mission. A low pass filter is included between the TC connector points and each MCP-9600 to help suppress spurious measurements.

5

### 2.2 Pressure Measurement

The KREPE-2 capsule design includes an array of ported pressure sensors in a cross configuration, constitutes what is known as a flushed air data sensing (FADS) system. Such FADS systems are very useful in the reconstruction of the re-entry trajectory attitude?. Flexible PTFE tubing is used to connect the hole in the forebody to the barb on the pressure sensor. An image of the Honeywell sensor used is shown in Fig. 4.

Figure 4: Honeywell ported pressure sensor used for the FADS system.

### 2.3 Spectrometer Subsystem

Another addition to the sensor suite on the KREPE-2 capsules is a Hamamatsu C12880 miniature spectrom-eter²
Due to the position that the spectrometer must be in, in the nose (stagnation point) of the capsule, there is a need for a processing element in the same region. For this reason we are working on implementing a Battery and Spectrometer Measurement System (BSMS). This BSMS will be able to read the spectrometer as well as monitor the system battery voltages.

### 2.4 Inertial Measurement

The KREPE-2 flight computer also features multiple inertial measurement sensors to collect rotational rates and accelerations experienced by the capsule during re-entry. Like FADS measurements, the IMU data collected by the capsule will also greatly aid the post-flight reconstruction of the re-entry environment which occurred for each capsule.
The inertial sensors present on the KREPE-2 flight computer are an FSM300, ICM-42670, and an H3LIS100. The FSM300 is a preassembled unit which features a BNO-088 9 axis IMU. The maximum acceleration measurable by the FSM300 is ±16g. The ICM-42670 is an additional 6-axis IMU included as an evaluation platform. The primary IMU is the FSM300. The H3LIS100 is a 3-axis accelerometer, included for measuring accelerations on the capsule which are greater than ±16g.

### 2.5 Power and Batteries

The power and battery subsystem on the KREPE-2 capsules has improved features and capacity from the KREPE-1 design. Batteries are still provided by NASA Cargo Mission Contract (CMC) fulfilled by JSC and rated at 3200mAh each. KREPE-2 features two separate battery packs which allow for greater flexibility when designing any future capsule instrumentation. Three cells are tabbed in series to provide a 3S1P pack (11.1V nominal), as well as a secondary system pack which consists of 3 cells tabbed in parallel, or 1S3P. The 3.7V pack powers the flight computer, but not any high-draw peripherals (GPS, Iridium modem, spectrometer, etc). The 11.1V pack is switched on after secondary activation and powers any high draw peripherals through an optional 5V buck regulator.
Battery classification, product, and model number can be seen in Fig. 2.5 (taken from battery specifica-tion sheet).

2https://www.hamamatsu.com/content/dam/hamamatsu-photonics/sites/documents/99_SALES_LIBRARY/ssd/c12880ma_

kacc1226e.pdf (https://www.hamamatsu.com/content/dam/hamamatsu-photonics/sites/documents/99_SALES_LIBRARY/ssd/c12880ma_kacc1226e.pdf)

6

Figure 5: Sanyo battery specifications from the datasheet.

The 3.7 pack is able to be recharged through the MCP73831³ present on the Feather M4, however the 11.1V pack currently be charged externally through a separate balance connector which does not connect to the flight computer.
There is work ongoing which aims to support the monitoring of the 3S1P pack. This system will also interface with the spectrometer.
Charging is only performed on the ground and there is no provision for charging in flight. Schematics and electrical connections are shown in Fig. 14 in Appendix A.

### 2.5.1 Battery Protection

Protection circuitry is implemented on each of the two battery packs present on the KREPE-2 capsules. We are using a DW01-P Voltage and Current Protection IC for the 3.7V and 11.1V system packs 4
The 11.1V auxiliary pack has a separate battery protection circuit that protects it from over current, under voltage, and over voltage conditions.


Figure 6: Battery protection circuitry.

Protection circuitry as implemented on the KREPE flight computer PCB is shown in Fig. 6. Our two battery packs are both connected to their respective battery protection circuitry, then to primary activation switches. This protection circuitry is upstream of the primary activation switch. The battery protection PCB can be seen in Fig. 7.

3
(https://www.microchip.com/wwwproducts/en/MCP73831) 4https://cdn.sparkfun.com/assets/learn_tutorials/2/5/1/DW01-P_DataSheet_V10.pdf

7

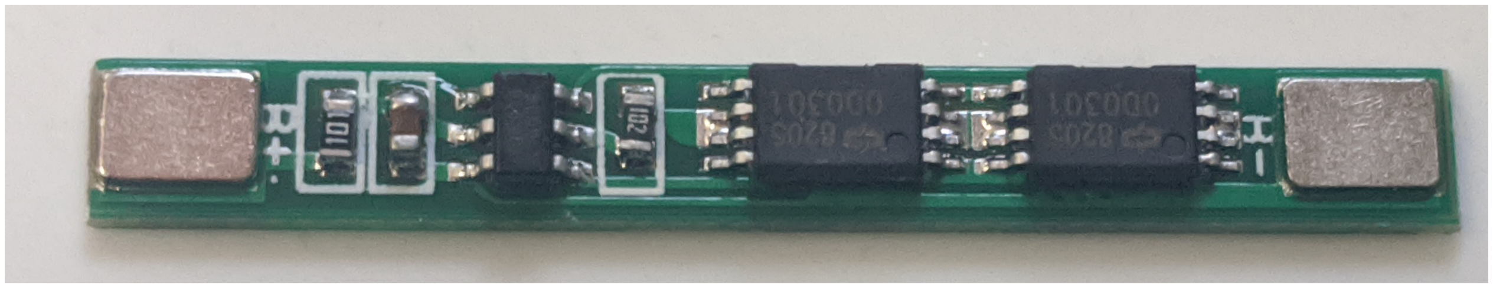
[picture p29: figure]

Figure 7: Battery protection PCB.

Over-current protection Both the 3.7V and 11.1 V packs have their own battery protection circuity as the first power function after the batteries and before any cabling goes to the avionics or flight computer. Pictures of the protection PCBs and overcurrent tests proving their effectiveness are shown in the following figures.

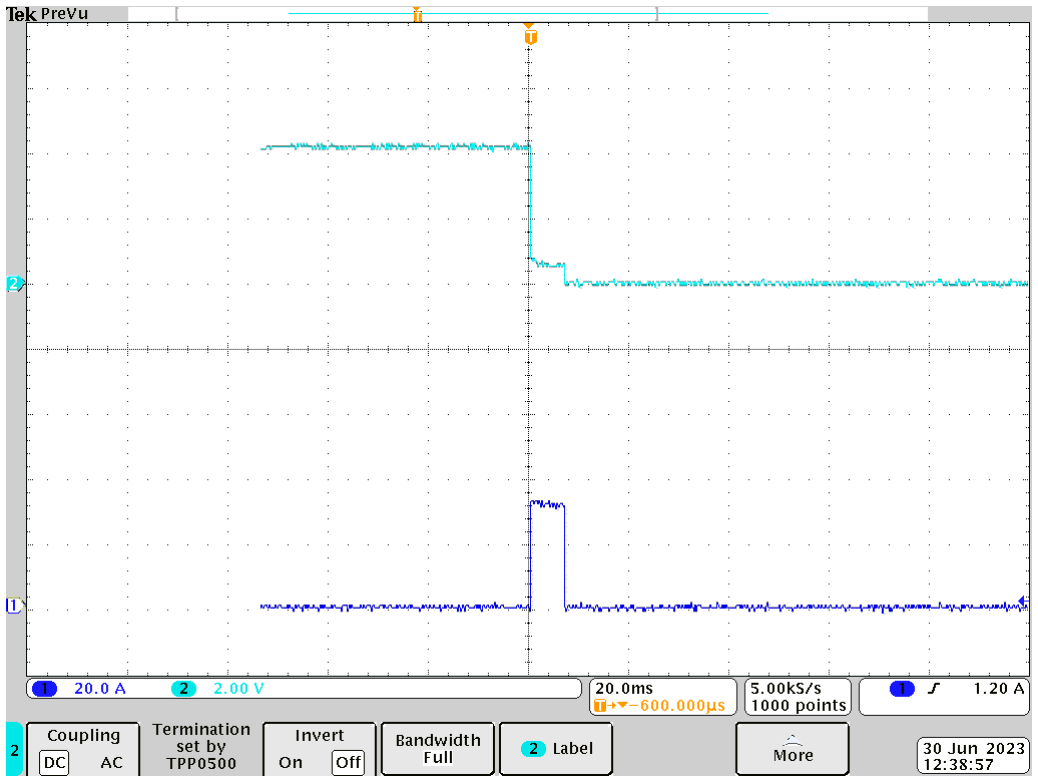
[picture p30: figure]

Figure 8: The battery protection circuity disconnecting the cells after 6ms of over current condition. Blue: current. Purple: pack voltage.

The high voltage pack (3S) is protected by another PCB that also uses the DW01 protection IC, except it has three of these chips in the same circuit in order to protect a 3S (series) pack from overvoltage, undervoltage, and overcurrent conditions. An example of the 11.1V pack protection circuitry protecting from over current conditions can be seen in Fig. 10. The circuit protection board for the three cell series pack can be seen in Fig. 9.

8

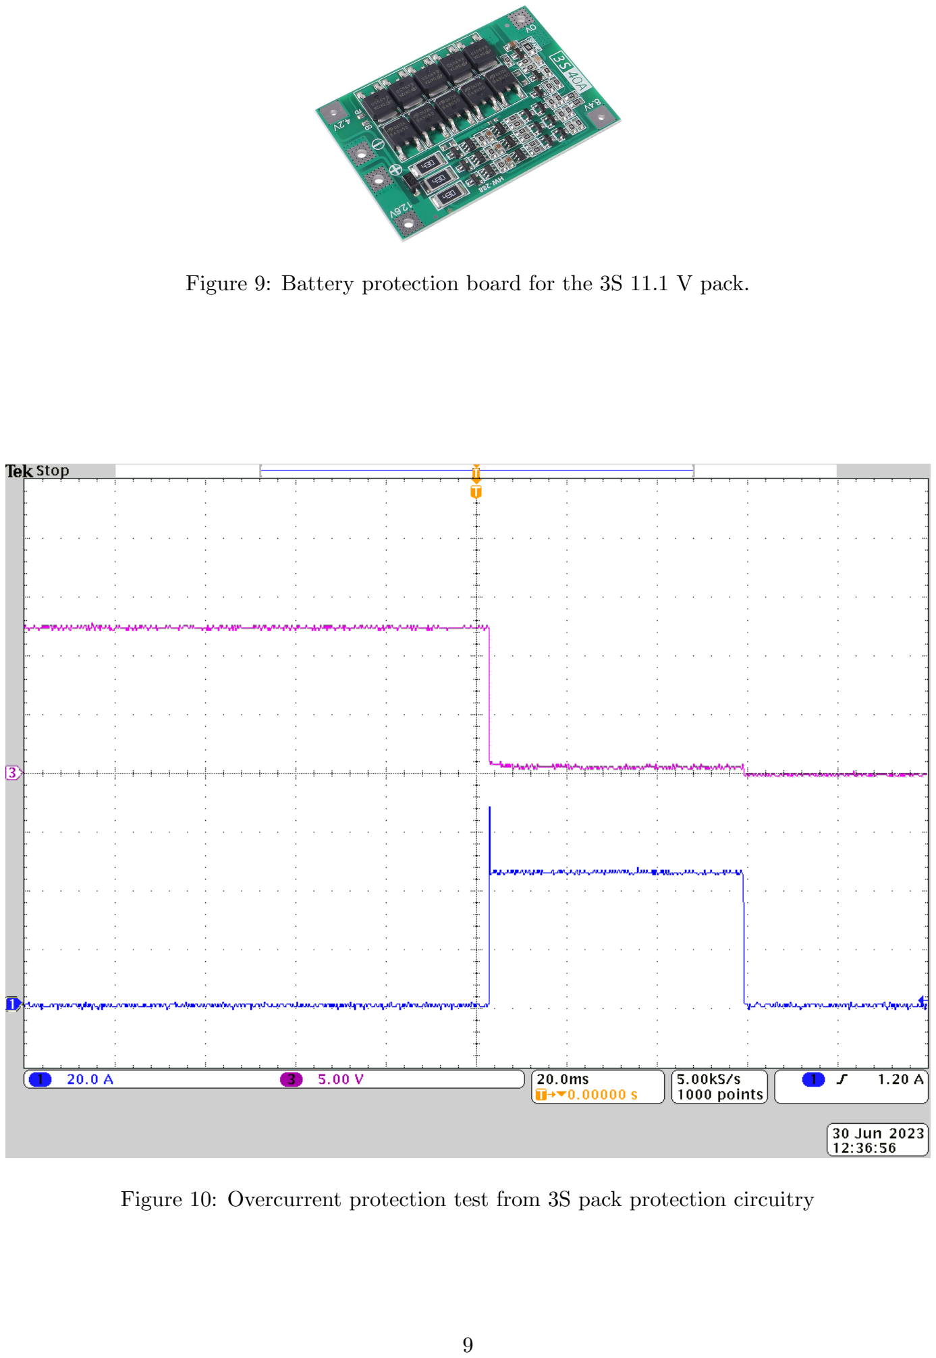
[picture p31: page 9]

Figure 9: Battery protection board for the 3S 11.1 V pack.

Figure 10: Overcurrent protection test from 3S pack protection circuitry

9

### 2.6 Visual Status Indicators

There are individual LEDs on the POL switches connected to each serial port header, in addition to an indicator on the external 3v3 regulator. In addition to these indicators, the Feather M4 board also has an RGB led that is used to indicate program state

## 3 PCB Assembly and Programming

### 3.1 Component placement and board bringup


Figure 11: A freshly assembled flight computer with tester attached. The tester performs I²C discovery and ensures all components are electrically connected

### 3.2 Solder Jumpers

There are several solder jumpers on the KFC.

- SJ8 selects which 3.3v source the RS232 translator chip will be powered from
- SJ10 selects the voltage source for the optionally level shifted UART (designated for GPS) to be either 5V or VIN (the high voltage pack)

10

- SJ11 selects the voltage source for the level shifted UART (designated for the Iridium modem) to be either 5V or VIN ( the high voltage pack).

### 3.3 Programming

## A Schematics

MOUNT-PMAODU-RNOT-UPNAMD2O-R.8UONUTN-PMDA2OD.8U-RNOT-UPNAD2-R.8OUND2.8

0.1uF

0.1uF

0.1uF

0.1uF

MOUNT-PMAODU-RNOT-UPNAD2-R.8OUND2.8

B4B-PH-K-S(LF)(SN)

B4B-PH-K-S(LF)(SN)

0.1uF

AQV252G 0.1uF

H1 | H2 | H3 | H4

C1+

1 | | | V+
2 | C1- 3 | C2+
4 | C2- 5 | V- 6 | T1OUT
7 | | | R1IN
8 | | | R1OUT

9 T1IN

10 T2IN

11 R2OUT

12 R2IN

13 T2OUT

14 GND

15 VCC

16 C6 | C⁷ C8

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
H6 H5

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
4 | SJ4
1 | 2 J5

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
SJ10

3 1
2

SJ11

3 1
2

C2

U3 LED+
1
LED- 2 | N/C
3 | SW+2
4 SW- | 5 SW+1

6 C3

JP12
1
2
3
4
5 | GND

GND

GND

GND

GND

GND | GND

GND

GND

GND

RIRI

T232 | TIRI
R232

3V3

SDA

SCL

TGPS

RGPS

R232_GPS

T232_GPS

5V

VBAT

VIN

VIN

TX_GPS

RX_GPS

GATE_IRIDIUM | VIN_PRE

VIN_PRE

VIN_PRE

Board to board connections

RS232 converter

Mounting holes

Depending on jumper settings, this port either provides access to a 3.3VTTL UART or the same UART

but shifted to RS232 levels

Rs232 level shifted UART for use with Iridium modem. Power rail select jumper for 5v regulator or raw VIN

3.3V TTL UART for connection to other subsystems or use as GPIO if no serial port needed.

I2C Header, intended to go to I2C mux for pressure sensors

PhotoMOS POL switch
for enabling 5V regulator connected to high voltage pack

Battery and power connections

Testpoints for system voltages VIN is the high voltage pack positive node

after being switched by the photoMOS

VIN_PRE is the high voltage pack positive node before being switched by the photoMOS

VBAT is the low voltage pack positive node

5V is the output node of the 5V regulator. The photoMOS must be enabled to supply this rail

connection to 5v regulator

Connection to high and low voltage battery packs.

flight-computer

Document Number: | REV:
Date: 1/12/23 2:33 PM | Sheet: 1/4

TITLE:

Figure 12: Page one of schematics.

11

VBUS

+3V3 GND

GND | GND | GND | GND

104031-0811

COM-13909 U.FL-R-SMT(10)

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
16 JP3
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
12 | U13 SPX3819-3.3
IN
1 | OUT

5 EN
3 | GND
2 | P4

4

J7 DAT2
1 CD/DAT3
2 CMD
3 | VDD

4 CLK

5 | VSS
6 DAT0

7 DAT1
8 GND | G1*4 SW-1
9 | SW-2
10 U1 | GND

1*3 DIO0

14 RESET

6
3.3V

13 MISO

2 | NSS
5 | SCK
4 | ANT
9 | DIO1

15 DIO2
16 DIO3
11 DIO4
12 MOSI 3 | DIO5

7

SJ6

3 1
2

J9

SJ9

1 2 JP⁴
1

2

JP5
1
2 | GND

GND

MOSI
MISO

MISO

SCK

SCK

TX4

RIRI
TIRI
RX4

AREF

SCL
SDA

RESET

RX1 | 3V32_CTRL
TX1

3V3

3V3

SD_CS

SD_CS

3V32

EXT_INT

EXT_INT

TGPS | TX_GPS | RGPS | RX_GPS

RADIO_INT

RADIO_INT

Feather M4 (SAMD51) headers | External 3v3 regulator
SD Card | I2C pull-up resistors

RFM69-HCW debug radio

A solder jumper and pin header connection are provided for controlling power to the radio. The radio should be disabled during

the actual mission.

The input to the regularor is connected to a solder jumper for selection between VBAT and the 5V rail. Choosing the 5V rail option means that even if the regulator is enabled with the

3V3_CTRL signal, the photoMOS mus also be on. These headers connect to a FeatherM4, mounted from the top of the PCB. Pins 9 and 10 of JP1 are connected to solder jumpers. Select TX_GPS and RX_GPS to bypass the RS232 level shifter IC. TGPS and RGPS connect the feather pins to teh RS232 shifter.

External activation header

This two pin header serves as a connection
point to the spring steel pieces that stick out of the
backshell and make contact with the KREM. When the KREM is intact,

the GPIO pin is shorted to ground. When the KREM separates, an interrupt is generated

flight-computer

Document Number: | REV:
Date: 1/12/23 2:33 PM | Sheet: 2/4

TITLE:

Figure 13: Page two of schematics.

12

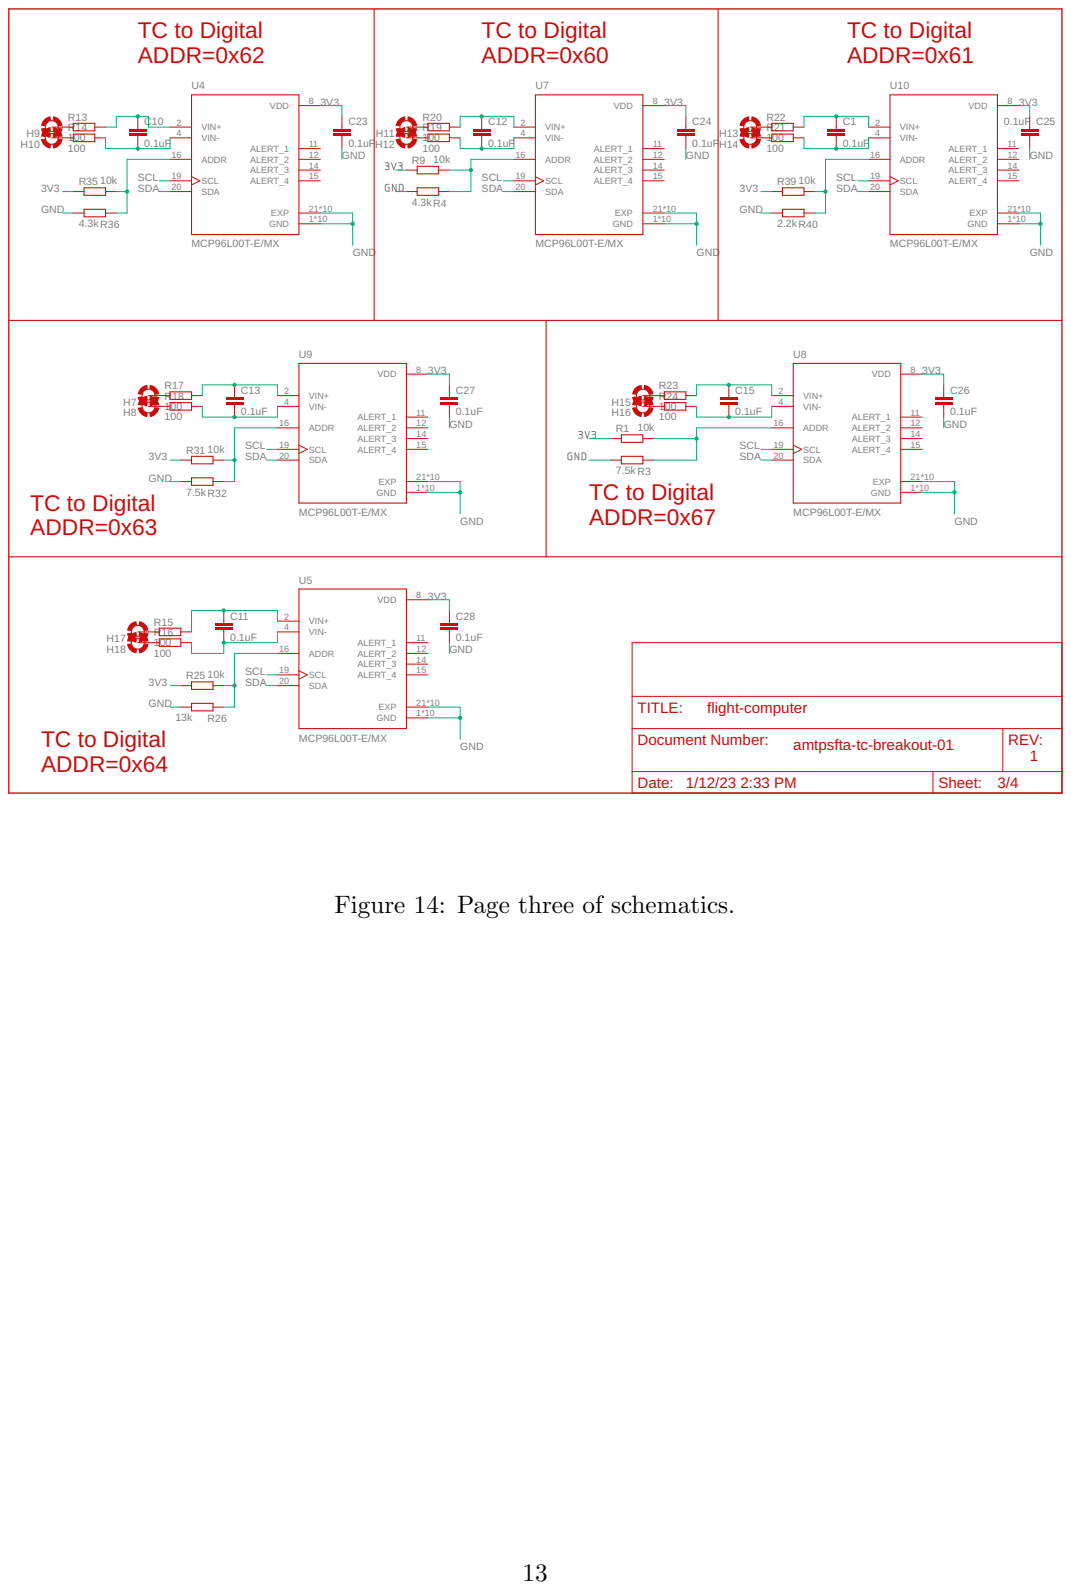
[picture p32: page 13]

ADDR=0x67 TC to Digital
ADDR=0x63

Document Number: amtpsfta-tc-breakout-01 | REV: 1

Date: 1/12/23 2:33 PM | Sheet: 3/4

Figure 14: Page three of schematics.

# 1 GND

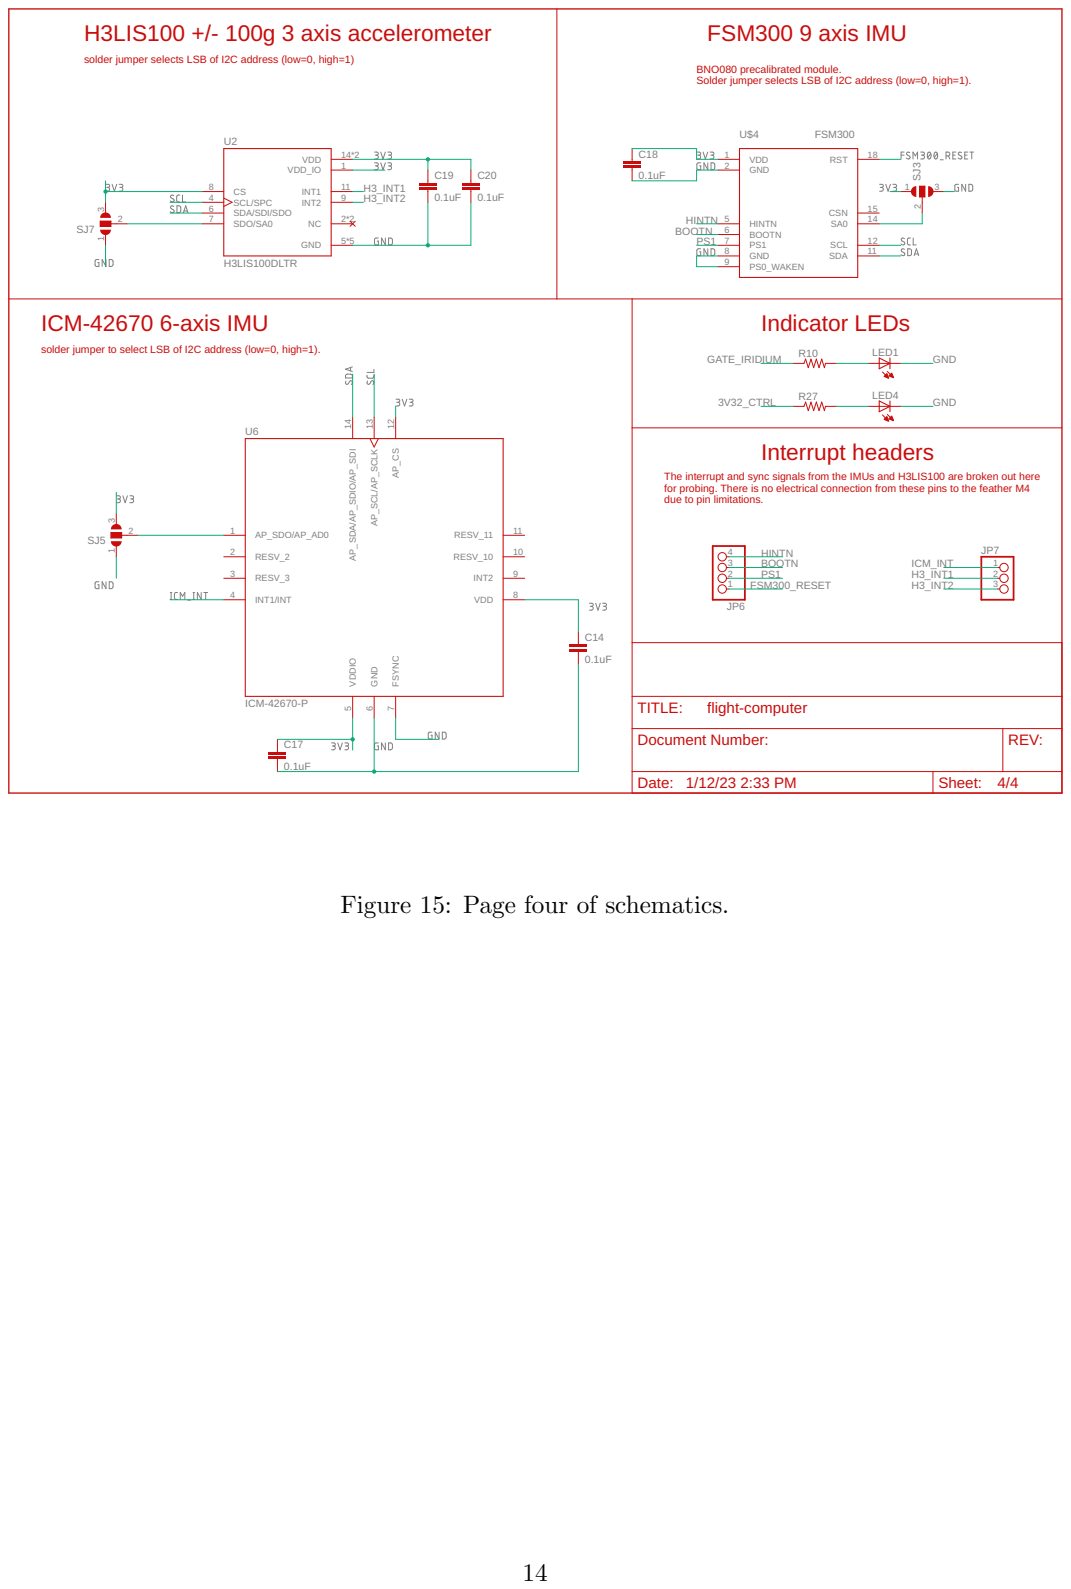
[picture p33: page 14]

BNO080 precalibrated module. Solder jumper selects LSB of I2C address (low=0, high=1). H3LIS100 +/- 100g 3 axis accelerometer

solder jumper selects LSB of I2C address (low=0, high=1)

The interrupt and sync signals from the IMUs and H3LIS100 are broken out here
for probing. There is no electrical connection from these pins to the feather M4
due to pin limitations.

Document Number: | REV:

Date: 1/12/23 2:33 PM | Sheet: 4/4

Figure 15: Page four of schematics.

## B Board Renderings

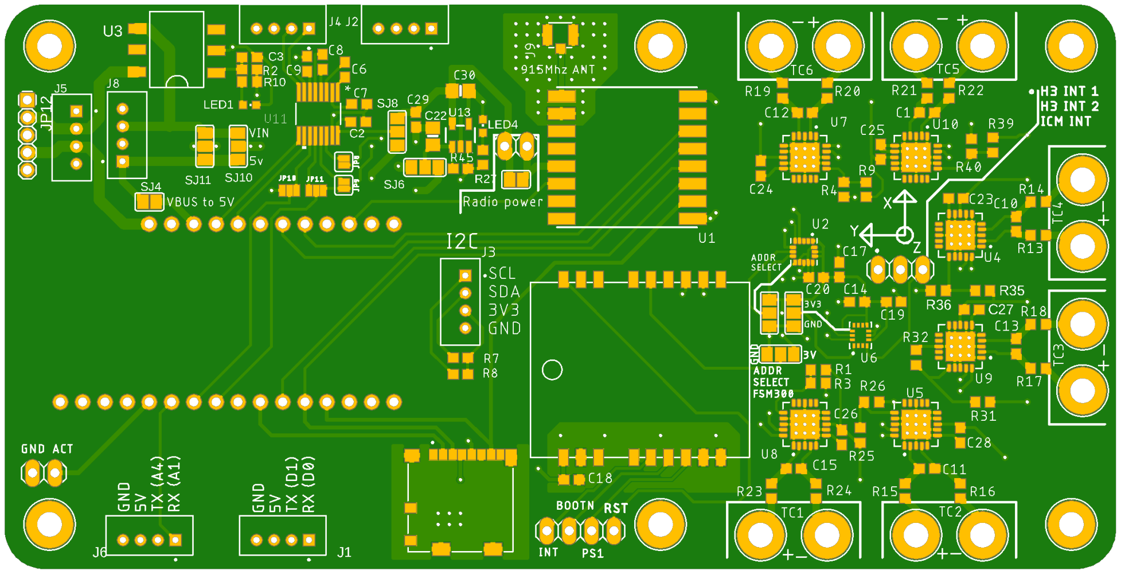
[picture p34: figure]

Figure 16: Rendering of the top of the KREPE-2 control board.

15

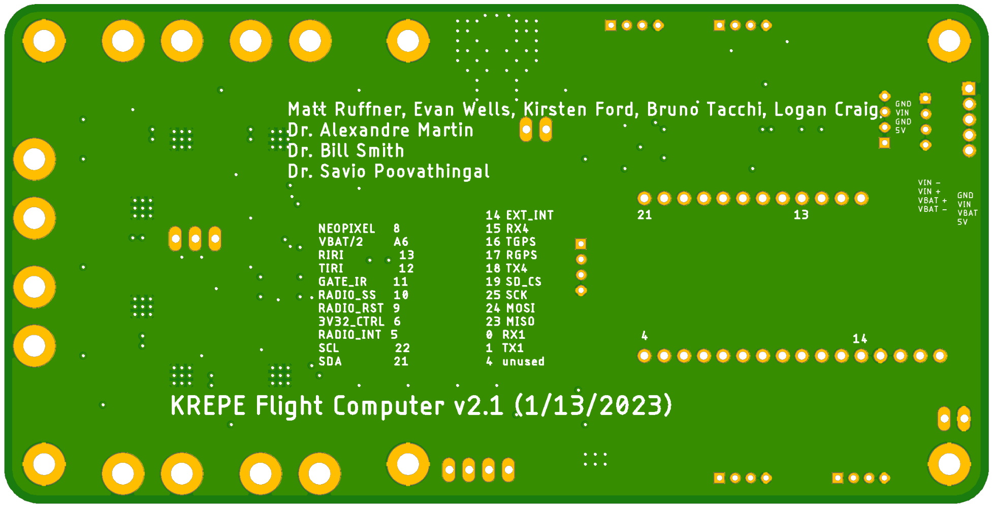
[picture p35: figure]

Figure 17: Rendering of the bottom of the KREPE-2 control board.

## C COTS hardware references

This section contains reference cards for the COTS components used in the KREPE-2 capsules.

16

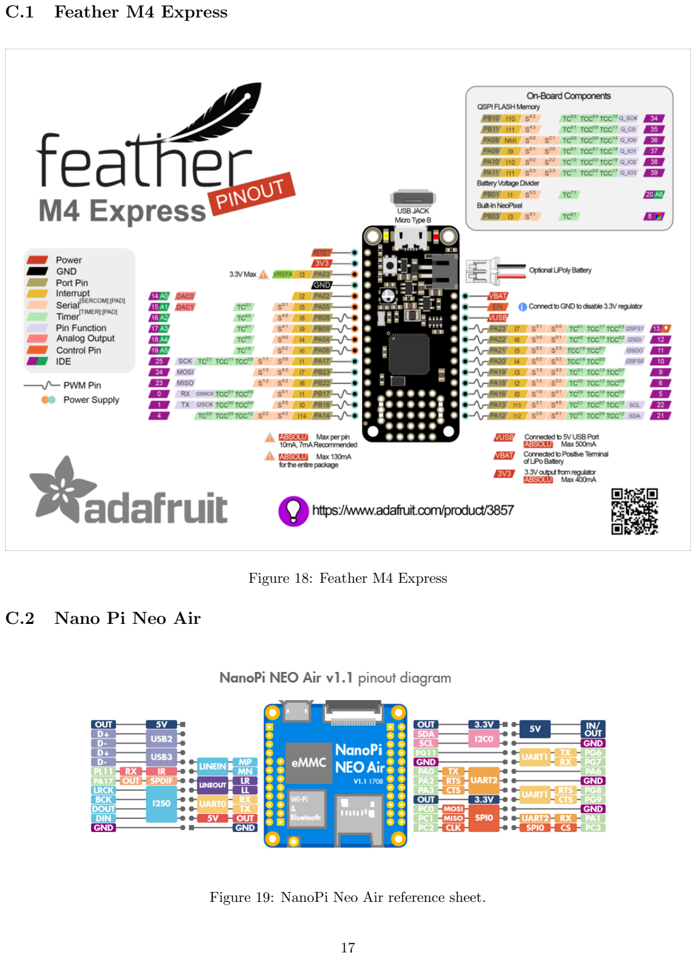
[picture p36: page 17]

C.1 Feather M4 Express

Figure 18: Feather M4 Express

C.2 Nano Pi Neo Air

Figure 19: NanoPi Neo Air reference sheet.

17

## D Partslist

P a r t l i s t

Expo r ted from | f l i g h t −computer . s c h | a t | 7/23/20 | 8 : 1 1 PM
EAGLE V e r s i o n | 9 . 6 . 2 | Co p y r ig h t | ( c ) 1988 −2020 Autodesk , | I n c .
Assembly | v a r i a n t :
Pa r t | Va lue | D e v i c e | Package | L i b r a r y | S h e e t
ACTIVATION SW | PINHD−1X2 | 1X02 | p i n h ea d | 3
ANT | U . FL−R−SMT−1(10) | U . FL−R−SMT−1(10) | CONN R−SMT−1(10) | u f l | 4
BATTERY | 2 PIN JST | S2B−PH−SM4−TB(LF ) ( SN) | JST S2B−PH−SM4−TB(LF ) ( SN) S2B−PH−SM4−TB LF | SN | 3
C1 | 10uF | C−EUC0603 | C0603 | r c l | 3
C2 | 1uF | C−EUC0603 | C0603 | r c l | 3
C3 | 0 . 1 uF | C−USC0603 | C0603 | a d a f r u i t | 2
C4 | 0 . 1 uF | C−USC0603 | C0603 | a d a f r u i t | 2
C5 | 0 . 1 uF | C−USC0603 | C0603 | a d a f r u i t | 2
C6 | 0 . 1 uF | C−USC0603 | C0603 | a d a f r u i t | 2
C7 | 1uF | CAP CERAMIC0603 NO | 0603−NO | m i c r o b u i l d e r | 5
C8 | 10uF | C−USC0603 | C0603 | a d a f r u i t | 1
C9 | 0 . 0 1 uF | C−USC0603 | C0603 | a d a f r u i t | 1
C10 | 0 . 0 1 uF | C−USC0603 | C0603 | a d a f r u i t | 1
C11 | 0 . 0 1 uF | C−USC0603 | C0603 | a d a f r u i t | 1
C12 | 0 . 1 uF | C−EUC0603 | C0603 | r c l | 4
C13 | 0 . 1 uF | C−EUC0603 | C0603 | r c l | 4
C14 | 0 . 1 uF | C−USC0603 | C0603 | a d a f r u i t | 3
C15 | 0 . 1 uF | C−EUC0603 | C0603 | r c l | 1
C16 | 0 . 1 uF | C−EUC0603 | C0603 | r c l | 1
C17 | 0 . 1 uF | C−EUC0603 | C0603 | r c l | 1
C18 | 0 . 1 uF | C−USC0603 | C0603 | r c l | 3
C19 | 2 . 2 uF | C−USC0603 | C0603 | r c l | 3
C20 | 0 . 0 1 uF | C−USC0603 | C0603 | r c l | 3
C22 | 1uF | C−EUC0603 | C0603 | r c l | 4
C24 | 0 . 0 1 uF | C−USC0603 | C0603 | a d a f r u i t | 2
C25 | 0 . 0 1 uF | C−USC0603 | C0603 | a d a f r u i t | 2
C26 | 0 . 0 1 uF | C−USC0603 | C0603 | a d a f r u i t | 2
C27 | 0 . 0 1 uF | C−USC0603 | C0603 | a d a f r u i t | 2
C28 | 0 . 0 1 uF | C−USC0603 | C0603 | a d a f r u i t | 2
C29 | 0 . 0 1 uF | C−USC0603 | C0603 | a d a f r u i t | 2
C30 | 0 . 0 1 uF | C−USC0603 | C0603 | a d a f r u i t | 2
C31 | 0 . 0 1 uF | C−USC0603 | C0603 | a d a f r u i t | 2
C32 | 0 . 1 uF | C−USC0603 | C0603 | a d a f r u i t | 2
C33 | 0 . 1 uF | C−USC0603 | C0603 | a d a f r u i t | 2
CAPSENSE | 53048 −0810 | 53048 −0810 | 53048 −0810 | con−molex−p i c o b l a d e | 4
CHARGE | PINHD−1X2 | 1X02 | p i n h ea d | 3
CHG | RED | LED−RED0603 | LED−0603 | SparkFun−LED | 3
CN1 | 4U#20329 | USB MICRO 20329 V2 | 4UCONN 20329 V2 | m i c r o b u i l d e r | 5
D3 | MBR120 | MBR120 | SOD123FL | g s y n t h | 3
H1 | MOUNT−PAD−ROUND2. 8 | MOUNT−PAD−ROUND2. 8 | 2 ,8−PAD | h o l e s | 1
H2 | MOUNT−PAD−ROUND2. 8 | MOUNT−PAD−ROUND2. 8 | 2 ,8−PAD | h o l e s | 1
H3 | MOUNT−PAD−ROUND2. 8 | MOUNT−PAD−ROUND2. 8 | 2 ,8−PAD | h o l e s | 1
H4 | MOUNT−PAD−ROUND2. 8 | MOUNT−PAD−ROUND2. 8 | 2 ,8−PAD | h o l e s | 1
H5 | MOUNT−PAD−ROUND2. 8 | MOUNT−PAD−ROUND2. 8 | 2 ,8−PAD | h o l e s | 1
H6 | MOUNT−PAD−ROUND2. 8 | MOUNT−PAD−ROUND2. 8 | 2 ,8−PAD | h o l e s | 1
IC1 | ADG609RU | ADG609RU | TSSOP16 | a na log−d e v i c e s | 2
IC2 | ATSAMD21E | ATSAMD21E | QFN32 5MM | m i c r o b u i l d e r | 5
IC3 | ADG609RU | ADG609RU | TSSOP16 | a na log−d e v i c e s | 2
JP1 | PINHD−1X4 | 1X04 | p i n h ea d | 5
JP2 | PINHD−1X2 | 1X02 | p i n h ea d | 3
JP3 | PINHD−1X2 | 1X02 | p i n h ea d | 4
LED1 | LEDCHIP−LED0603 | CHIP−LED0603 | a d a f r u i t | 4
LED2 | LEDCHIP−LED0603 | CHIP−LED0603 | a d a f r u i t | 4
LED3 | LEDCHIP−LED0603 | CHIP−LED0603 | a d a f r u i t | 4
LED4 | LEDCHIP−LED0603 | CHIP−LED0603 | a d a f r u i t | 4
LED5 | LEDCHIP−LED0603 | CHIP−LED0603 | a d a f r u i t | 4
P1 | 53048 −0810 | 53048 −0810 | 53048 −0810 | con−molex−p i c o b l a d e | 2
P2 | 53048 −0810 | 53048 −0810 | 53048 −0810 | con−molex−p i c o b l a d e | 2
R1 | 1k | R−US R0603 | R0603 | r c l | 3
R2 | 2 . 2 k | R−US R0603 | R0603 | r c l | 3
R3 | 288 | R−US R0603 | R0603 | a d a f r u i t | 3
R4 | 470 | R−US R0603 | R0603 | r c l | 4
R5 | 100 k | R−US R0603 | R0603 | r c l | 3
R6 | 100 k | R−US R0603 | R0603 | r c l | 3
R7 | 100 k | R−US R0603 | R0603 | r c l | 3
R8 | 470 | R−US R0603 | R0603 | r c l | 4
R9 | 470 | R−US R0603 | R0603 | r c l | 4
R10 | 470 | R−US R0603 | R0603 | r c l | 4
R11 | 470 | R−US R0603 | R0603 | r c l | 4
R12 | 2 . 2 k | R−US R0603 | R0603 | r c l | 1
R13 | 200 k | R−US R0603 | R0603 | r c l | 1
R14 | 2 . 2 k | R−US R0603 | R0603 | r c l | 1
R15 | 2 . 2 k | R−US R0603 | R0603 | r c l | 1
R16 | 2 . 2 k | R−US R0603 | R0603 | r c l | 1
R17 | 10 k | R−US R0603 | R0603 | r c l | 5
R18 | 100 k | R−US R0603 | R0603 | r c l | 3
R19 | 100 | R−US R0603 | R0603 | r c l | 4
SJ1 | SJ | SJ | jumper | 5
U$1 | TEENSY 3 . 5 / 3 . 6 BASIC TEENSY 3 . 5 / 3 . 6 BASIC | TEENSY 3 . 5 / 3 . 6 BASIC | Teen sy356 | 1
U$29 | AQV252GA | AQV252GA | DIP6 | T I r a d i o | 3
U1 | MCP73831/OT | MCP73831/OT | SOT23−5L | a d a f r u i t | 3
U2 | LP2985IM5 −1 .8/NOPB | LP2985IM5 −1 .8/NOPB | MF05A | g s y n t h | 3
U3 | COM−13909 | COM−13909 | MOD COM−13909 | COM−13909 | 4
U4 | ADXL377 | ACCEL ADXL377 | LFCSP16 LQ | m i c r o b u i l d e r | 1
U5 | ICM−20948 | ICM−20948 | QFN40P300X300X105−25N | ICM−20948 | 1
U6 | PCA9306DCUR | PCA9306DCUR | DCU8 | g s y n t h | 1
U7 | SN74LVC1T45DRLR | SN74LVC1T45DRLR | DRL6 | g s y n t h | 1
U8 | SN74LVC1T45DRLR | SN74LVC1T45DRLR | DRL6 | g s y n t h | 1
U9 | DMP3099L | DMP3099L | SOT23 | g s y n t h | 3

18

U10 | SN74LVC1G08DCKR | SN74LVC1G08DCKR | SOT65P210X110−5N | SN74LVC1G08DCKR | 5
U11 | DPS310XTSA1 | DPS310XTSA1 | XDCR DPS310XTSA1 | DPS310XTSA1 | 4
U12 | MAX31856MUD+ | MAX31856MUD+ | SOP65P640X110−14N | MAX31856 | 2
U13 | MAX31856MUD+ | MAX31856MUD+ | SOP65P640X110−14N | MAX31856 | 2
VBAT PTH | | PINHD−1X2 | 1X02 | p i n h ea d | 3
X3 | HEADER POS6 43650−0600 43650 −0600 | con−molex−m icro−f i t −3 0 3

19

## E Arduino Pin Mapping

Arduino Pin | Net

Teensy 3. 5
0 | CAPSENSE0
1 | CAPSENSE1
3 | LED IRIDIUM ON
4 | LED IRIDIUM SIGNAL OK
5 | LED IRIDIUM TRANSMITTING
6 | LED ISM TRANSMITTING
7 | LED ACTIVITY
8 | CS DSP
9 | CS ISM
11 | MOSI
12 | MISO
13 | SCLK
14 | BAT STAT
15 | CAPSENSE2
16 | MUX0
17 | MUX1
18 | SDA
19 | SCL
20 | CS@TC1
21 | CS@TC2
A8 | BAT SENSE (A8)
23 | PRI ACT ( IRIDIUM ON/OFF)
24 | BUZZER
25 | TC1 FAULT (ACTIVE LOW)
26 | TC2 FAULT (ACTIVE LOW)
27 | SEC CTRL 2
28 | RESET ISM
28 | INT ISM
30 | CAPSENSE3
31 | RIRI ( IRIDIUM OUTPUT)
32 | TIRI ( IRIDIUM INPUT)
33 | RADIO OFF SIG
34 | FSYNC (IMU)
35 | INT (IMU)
36 | XOUT (A17 )
37 | YOUT (A18 )
38 | ZOUT (A19 )
39 | SEC CTRL 1
A21 | IRIDIUM TX ACT
A22 | IRIDIUM STATUS

S a f e t y P r o c e s s o r (ATSAMD21E16B)
1 | CS@TC1
13 | CS@TC2
7 | SEC ACT
8 | SEC CTRL 1

20

0 | SEC CTRL 2
PA14 | TC1 FAULT
PA15 | TC2 FAULT
PA17 | MUX0
PA18 | MUX1

21

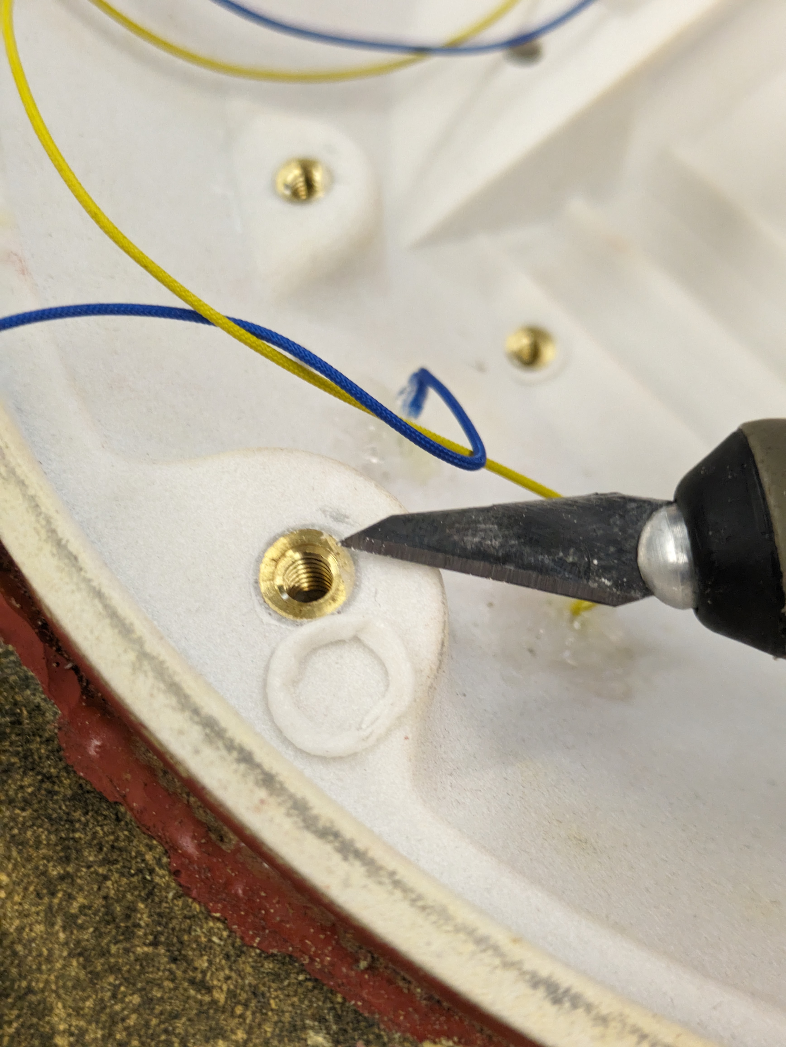
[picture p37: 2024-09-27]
doc/images/krepe2build/heat_insert4.jpg

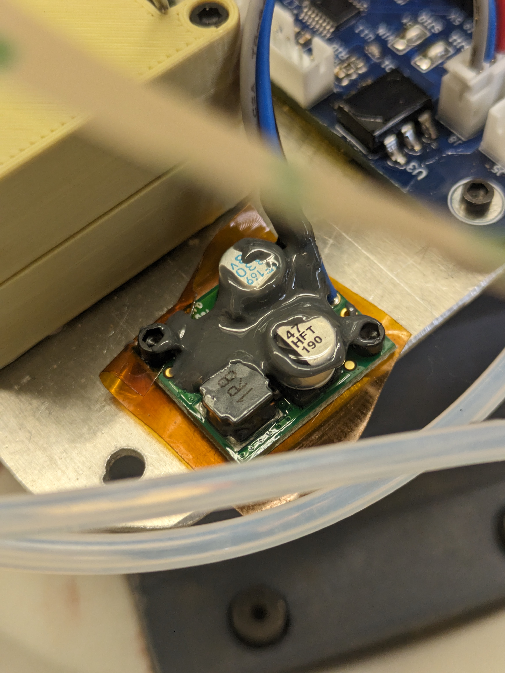
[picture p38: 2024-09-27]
doc/images/krepe2build/5vreg.jpg

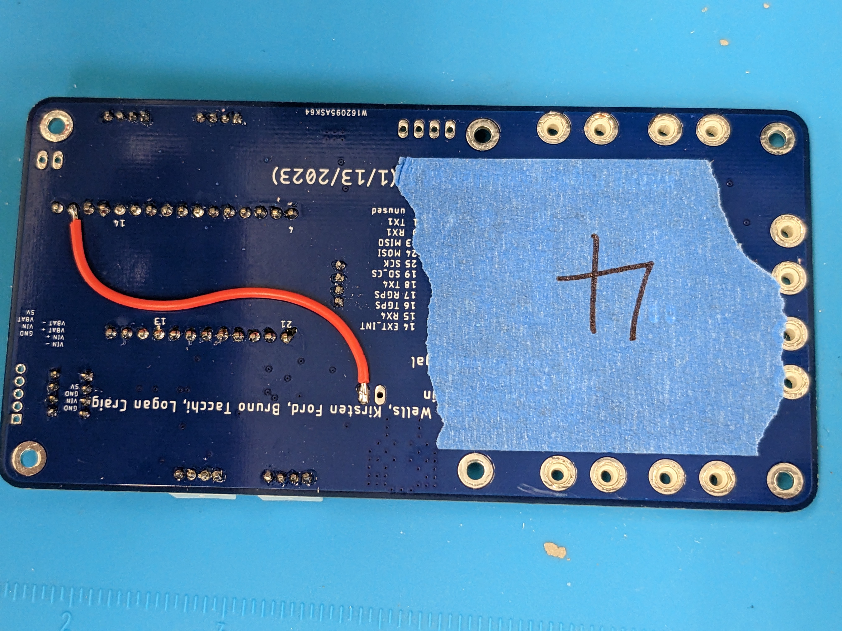
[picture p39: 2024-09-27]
doc/images/krepe2build/3v3patch.jpg

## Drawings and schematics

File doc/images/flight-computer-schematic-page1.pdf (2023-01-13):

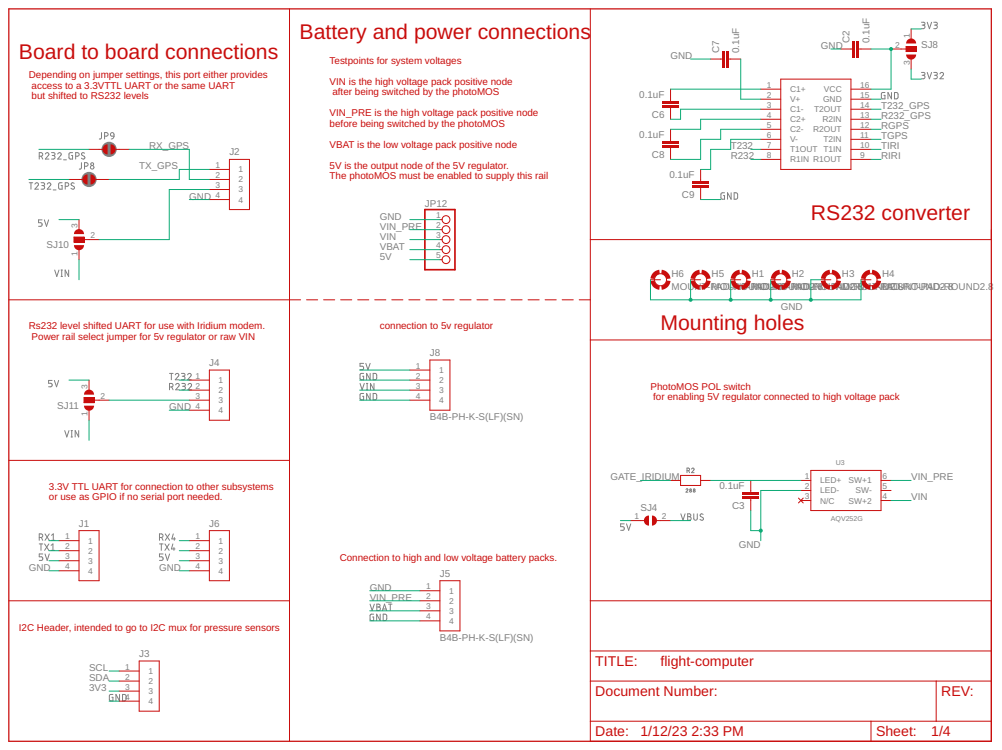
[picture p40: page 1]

Battery and power connections

Board to board connections

Testpoints for system voltages VIN is the high voltage pack positive node

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

MOUNT-PMAODU-RNOT-UPNAMD2O-R.8UONUTN-PMDA2OD.8U-RNOT-UPNAD2-R.8OUND2.8

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

PhotoMOS POL switch
for enabling 5V regulator connected to high voltage pack

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

Connection to high and low voltage battery packs.

I2C Header, intended to go to I2C mux for pressure sensors

Document Number: | REV:

Date: 1/12/23 2:33 PM | Sheet: 1/4

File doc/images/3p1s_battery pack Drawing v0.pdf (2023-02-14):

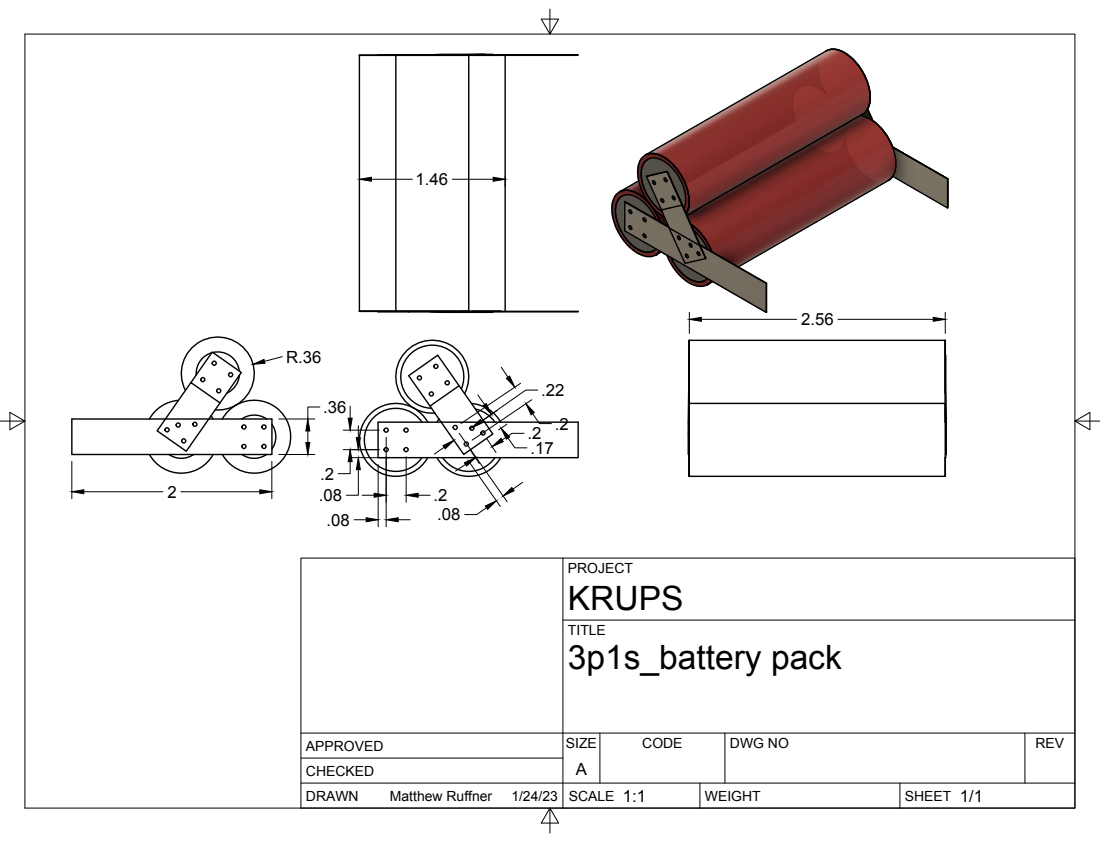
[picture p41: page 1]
SIZE; CODE; DWG NO; REV; Matthew Ruffner; 3p1s_battery pack

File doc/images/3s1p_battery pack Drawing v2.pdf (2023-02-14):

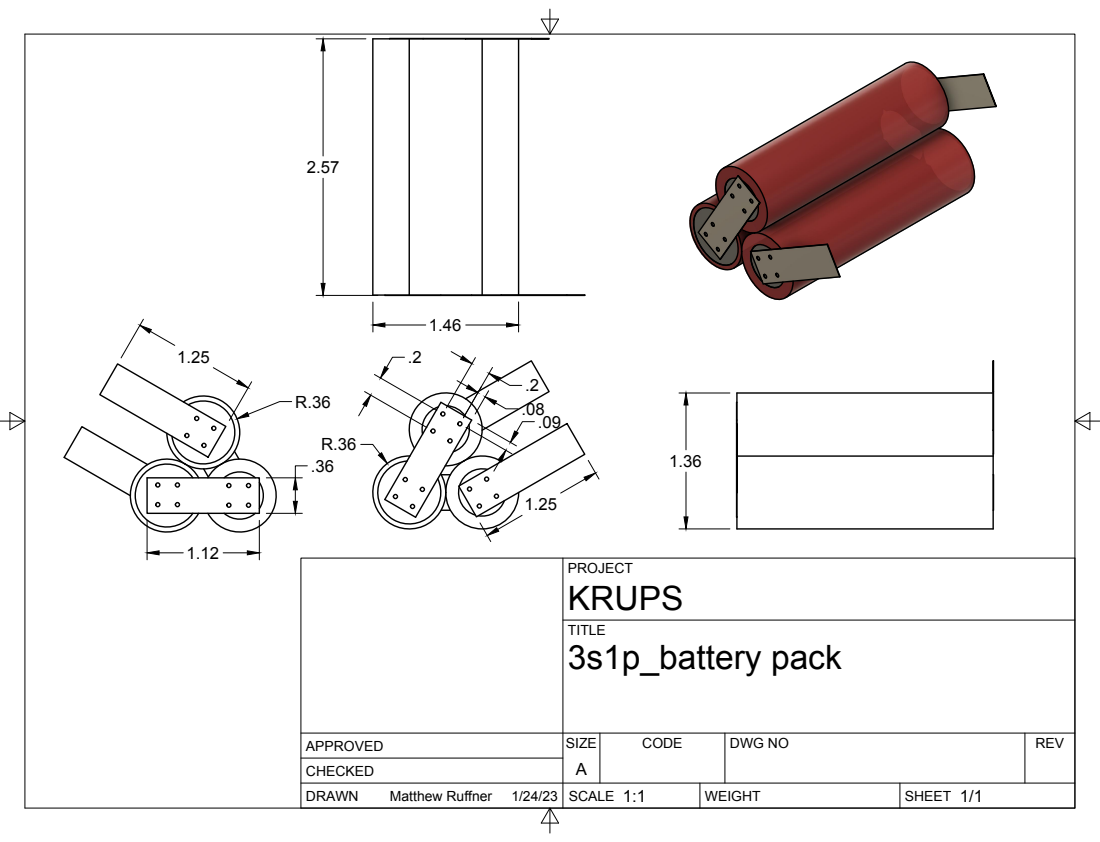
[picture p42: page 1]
SIZE; CODE; DWG NO; REV; Matthew Ruffner; 3s1p_battery pack

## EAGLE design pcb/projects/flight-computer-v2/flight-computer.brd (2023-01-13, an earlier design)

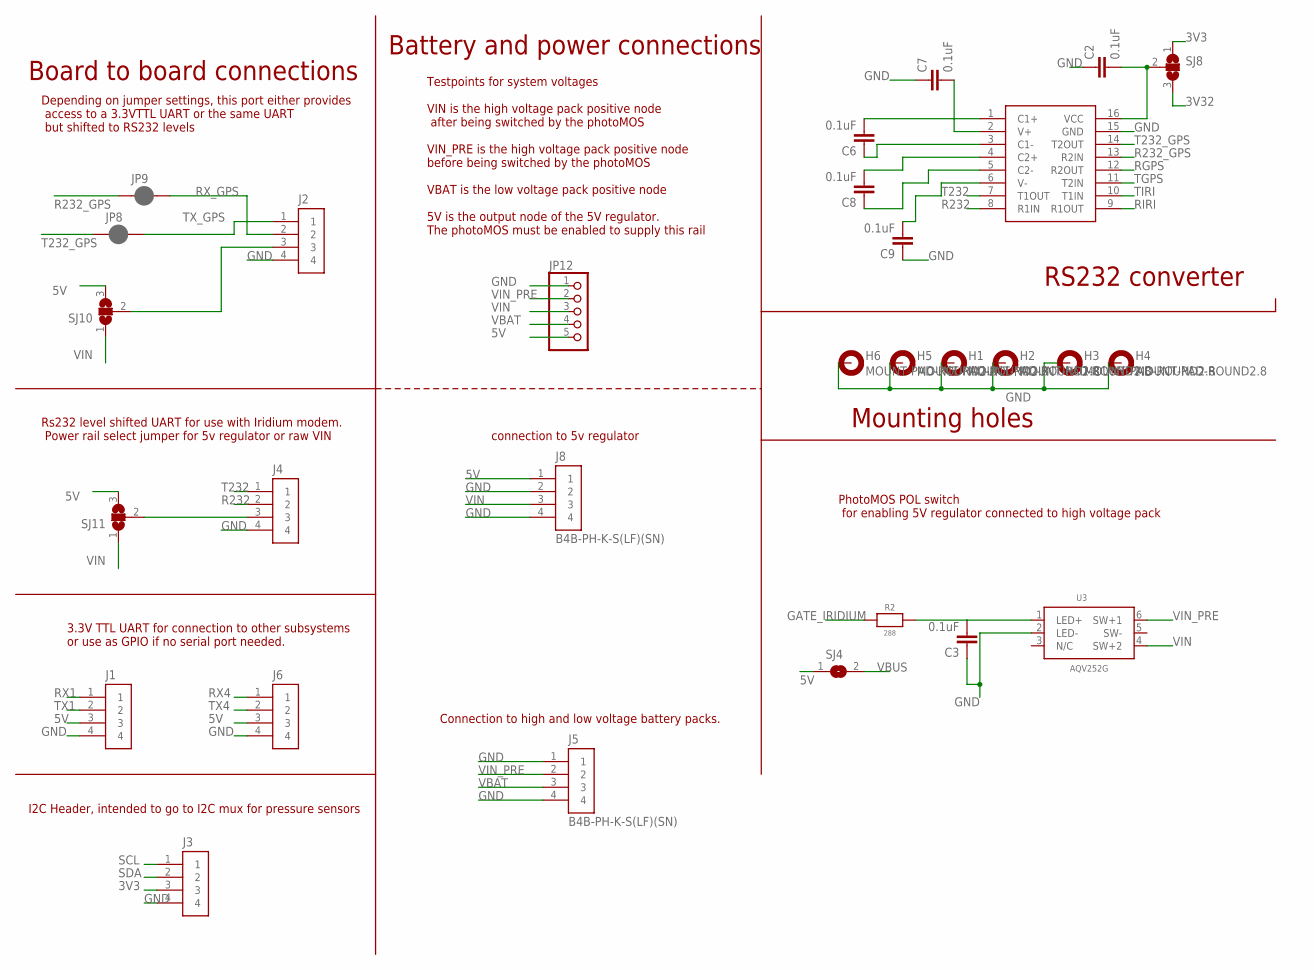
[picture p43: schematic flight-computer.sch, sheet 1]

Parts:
C2, C3, C6, C7, C8, C9: 0.1uF; C0603
H1, H2, H3, H4, H5, H6: MOUNT-PAD-ROUND2.8; 2,8-PAD
J1, J2, J3, J4, J5, J6, J8: B4B-PH-K-S(LF)(SN); JST_B4B-PH-K-S(LF)(SN)
JP8, JP9: JUMPER-SMT_2_NC_PASTE_SILK; SMT-JUMPER_2_NC_PASTE_SILK
JP12: PINHD-1X55X2MM; 1_05X2MM
R2: 288; 0603-NO
SJ4: SJ
SJ8, SJ10, SJ11: SJ2W; SJ_2
U3: AQV252G; SOP6
U11: UM3232EEAE; RQ_16_ADI

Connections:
3V3: J3.3, SJ8.1; also elsewhere on the board
3V32: SJ8.3; also elsewhere on the board
5V: J1.3, J6.3, J8.1, JP12.5, SJ4.1, SJ10.3, SJ11.3; also elsewhere on the board
GATE_IRIDIUM: R2.1; also elsewhere on the board
GND: C2.1, C3.1, C7.1, C9.1, H1.B2,8, H2.B2,8, H3.B2,8, H4.B2,8, H5.B2,8, H6.B2,8, J1.4, J2.4, J3.4, J4.4, J5.1, J5.4, J6.4, J8.2, J8.4, JP12.1, U3.2 (LED-), U11.15 (GND); also elsewhere on the board
unnamed: C6.2, U11.1 (C1+)
unnamed: J2.3, SJ10.2
unnamed: C2.2, SJ8.2, U11.16 (VCC)
unnamed: C7.2, U11.2 (V+)
unnamed: C6.1, U11.3 (C1-)
unnamed: C8.2, U11.4 (C2+)
unnamed: C8.1, U11.5 (C2-)
unnamed: C9.2, U11.6 (V-)
unnamed: J4.3, SJ11.2
unnamed: C3.2, R2.2, U3.1 (LED+)
R232: J4.2, U11.8 (R1IN)
R232_GPS: JP9.1, U11.13 (R2IN)
RGPS: U11.12 (R2OUT); also elsewhere on the board
RIRI: U11.9 (R1OUT); also elsewhere on the board
RX1: J1.1; also elsewhere on the board
RX4: J6.1; also elsewhere on the board
RX_GPS: J2.2, JP9.2; also elsewhere on the board
SCL: J3.1; also elsewhere on the board
SDA: J3.2; also elsewhere on the board
T232: J4.1, U11.7 (T1OUT)
T232_GPS: JP8.1, U11.14 (T2OUT)
TGPS: U11.11 (T2IN); also elsewhere on the board
TIRI: U11.10 (T1IN); also elsewhere on the board
TX1: J1.2; also elsewhere on the board
TX4: J6.2; also elsewhere on the board
TX_GPS: J2.1, JP8.2; also elsewhere on the board
VBAT: J5.3, JP12.4; also elsewhere on the board
VBUS: SJ4.2; also elsewhere on the board
VIN: J8.3, JP12.3, SJ10.1, SJ11.1, U3.4 (SW+2)
VIN_PRE: J5.2, JP12.2, U3.6 (SW+1)

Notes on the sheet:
Board to board connections
RS232 converter
Mounting holes
Depending on jumper settings, this port either provides access to a 3.3VTTL UART or the same UART but shifted to RS232 levels
Rs232 level shifted UART for use with Iridium modem. Power rail select jumper for 5v regulator or raw VIN
3.3V TTL UART for connection to other subsystems or use as GPIO if no serial port needed.
I2C Header, intended to go to I2C mux for pressure sensors
PhotoMOS POL switch for enabling 5V regulator connected to high voltage pack
Battery and power connections
Testpoints for system voltages VIN is the high voltage pack positive node after being switched by the photoMOS VIN_PRE is the high voltage pack positive node before being switched by the photoMOS VBAT is the low voltage pack positive node 5V is the output node of the 5V regulator. The photoMOS must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
connection to 5v regulator
Connection to high and low voltage battery packs.

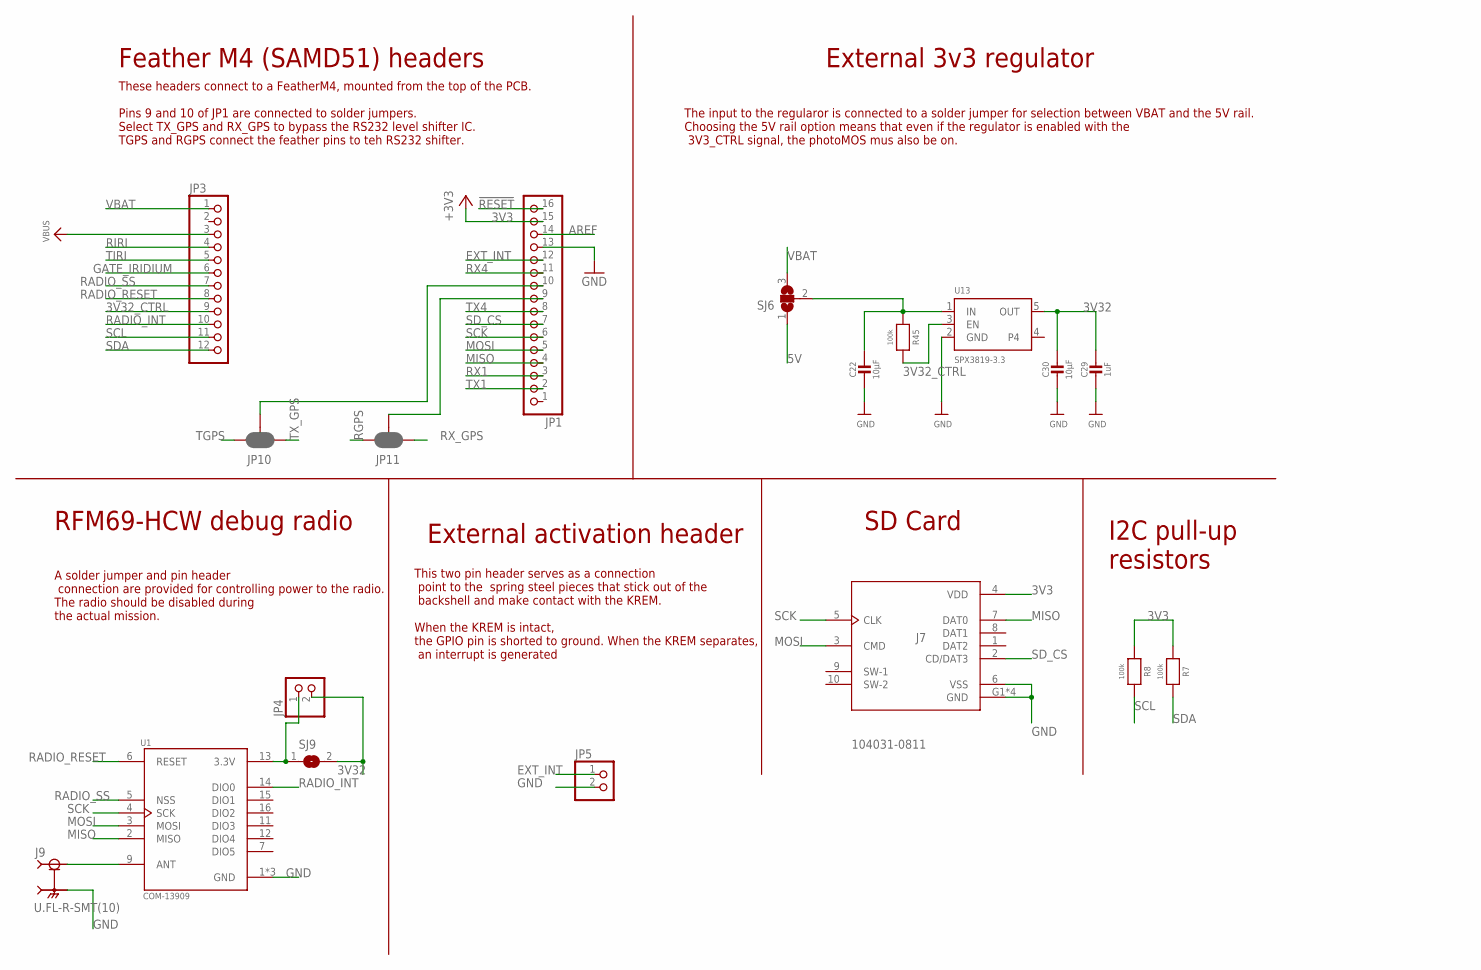
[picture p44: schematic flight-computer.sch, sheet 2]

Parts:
C22, C30: 10µF; 0805-NO
C29: 1uF; 0603-NO
J7: 104031-0811; MOLEX_104031-0811
J9: U.FL-R-SMT(10); HRS_U.FL-R-SMT(10)
JP1: HEADER-1X16ROUND; 1X16_ROUND
JP3: HEADER-1X12; 1X12_ROUND
JP4, JP5: PINHD-1X2; 1X02
JP10, JP11: JUMPER-SMT_3_2-NC_PASTE_NO-SILK; SMT-JUMPER_3_2-NC_PASTE_NO-SILK
R7, R8, R45: 100k; 0603-NO
SJ6: SJ2W; SJ_2
SJ9: SJ
U1: COM-13909; MOD_COM-13909
U13: SPX3819-3.3; SOT23-5

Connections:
3V3: J7.4 (VDD), JP1.15, R7.1, R8.1; also elsewhere on the board
3V32: C29.1, C30.1, JP4.2, SJ9.2, U13.5 (OUT); also elsewhere on the board
3V32_CTRL: JP3.9, R45.2, U13.3 (EN); also elsewhere on the board
5V: SJ6.1; also elsewhere on the board
!RESET: JP1.16
AREF: JP1.14
EXT_INT: JP1.12, JP5.1
GATE_IRIDIUM: JP3.6; also elsewhere on the board
GND: C22.2, C29.2, C30.2, J7.6 (VSS), J7.G1 (GND), J7.G2 (GND), J7.G3 (GND), J7.G4 (GND), J9.2 (GND), J9.3 (GND), JP1.13, JP5.2, U1.1 (GND), U1.8 (GND), U1.10 (GND), U13.2 (GND); also elsewhere on the board
MISO: J7.7 (DAT0), JP1.4, U1.2 (MISO)
MOSI: J7.3 (CMD), JP1.5, U1.3 (MOSI)
unnamed: JP4.1, SJ9.1, U1.13 (3.3V)
unnamed: C22.1, R45.1, SJ6.2, U13.1 (IN)
unnamed: J9.1 (SIG), U1.9 (ANT)
unnamed: JP1.10, JP10.2
unnamed: JP1.9, JP11.2
RADIO_INT: JP3.10, U1.14 (DIO0)
RADIO_RESET: JP3.8, U1.6 (RESET)
RADIO_SS: JP3.7, U1.5 (NSS)
RGPS: JP11.3; also elsewhere on the board
RIRI: JP3.4; also elsewhere on the board
RX1: JP1.3; also elsewhere on the board
RX4: JP1.11; also elsewhere on the board
RX_GPS: JP11.1; also elsewhere on the board
SCK: J7.5 (CLK), JP1.6, U1.4 (SCK)
SCL: JP3.11, R8.2; also elsewhere on the board
SDA: JP3.12, R7.2; also elsewhere on the board
SD_CS: J7.2 (CD/DAT3), JP1.7
TGPS: JP10.3; also elsewhere on the board
TIRI: JP3.5; also elsewhere on the board
TX1: JP1.2; also elsewhere on the board
TX4: JP1.8; also elsewhere on the board
TX_GPS: JP10.1; also elsewhere on the board
VBAT: JP3.1, SJ6.3; also elsewhere on the board
VBUS: JP3.3; also elsewhere on the board

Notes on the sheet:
Feather M4 (SAMD51) headers
External 3v3 regulator
SD Card
I2C pull-up resistors
RFM69-HCW debug radio
A solder jumper and pin header connection are provided for controlling power to the radio. The radio should be disabled during the actual mission.
The input to the regularor is connected to a solder jumper for selection between VBAT and the 5V rail. Choosing the 5V rail option means that even if the regulator is enabled with the 3V3_CTRL signal, the photoMOS mus also be on.
These headers connect to a FeatherM4, mounted from the top of the PCB. Pins 9 and 10 of JP1 are connected to solder jumpers. Select TX_GPS and RX_GPS to bypass the RS232 level shifter IC. TGPS and RGPS connect the feather pins to teh RS232 shifter.
External activation header
This two pin header serves as a connection point to the spring steel pieces that stick out of the backshell and make contact with the KREM. When the KREM is intact, the GPIO pin is shorted to ground. When the KREM separates, an interrupt is generated

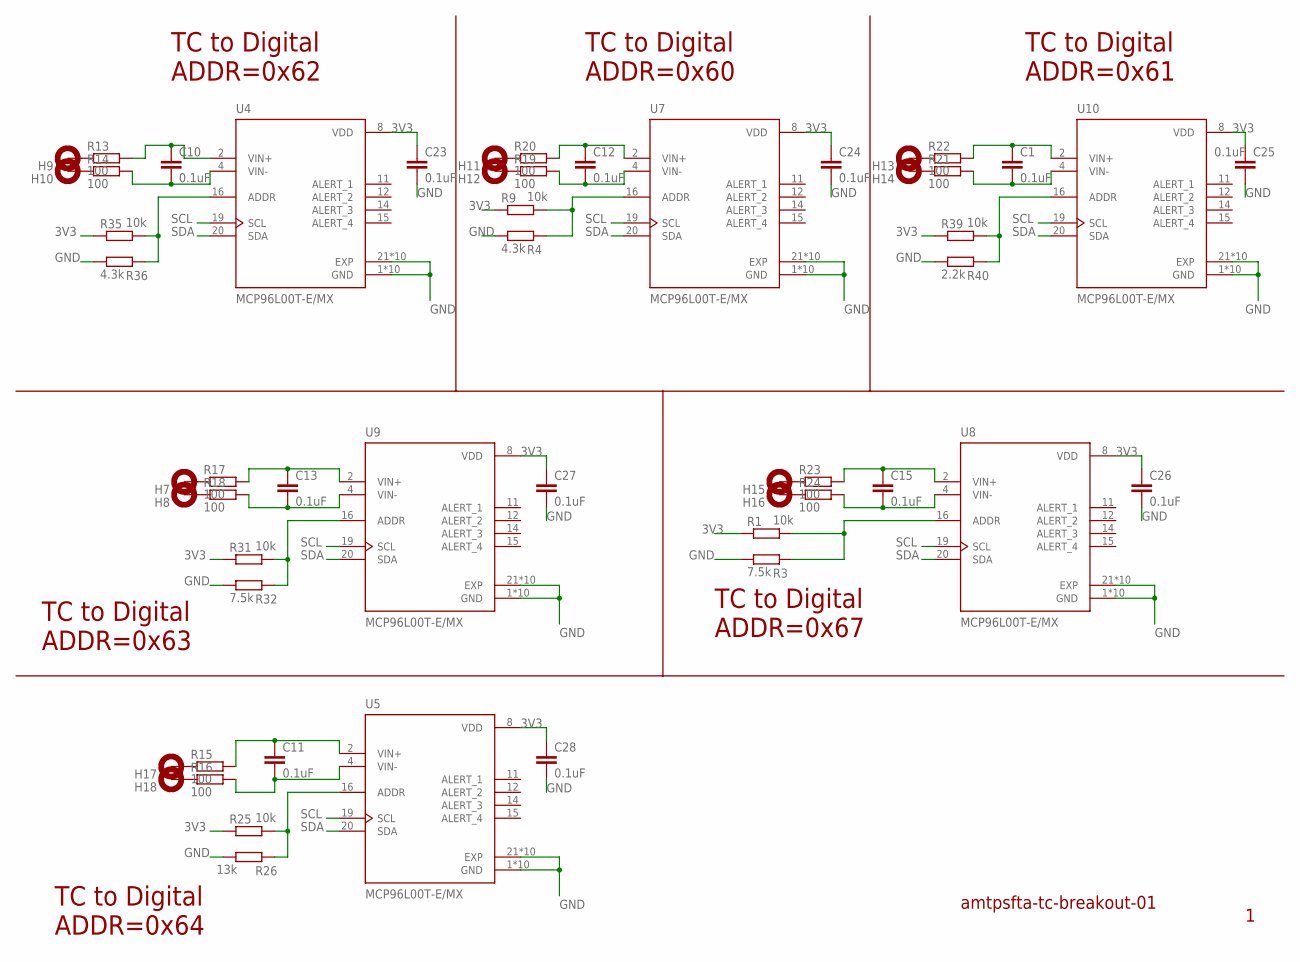
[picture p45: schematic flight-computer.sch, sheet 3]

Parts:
C1, C10, C11, C12, C13, C15, C23, C24, C25, C26, C27, C28: 0.1uF; C0603
H7, H8, H9, H10, H11, H12, H13, H14, H15, H16, H17, H18: MOUNT-PAD-ROUND2.8; 2,8-PAD
R1, R9, R25, R31, R35, R39: 10k; R0603
R3, R32: 7.5k; R0603
R4, R36: 4.3k; R0603
R13, R14, R15, R16, R17, R18, R19, R20, R21, R22, R23, R24: 100; R0603
R26: 13k; R0603
R40: 2.2k; R0603
U4, U5, U7, U8, U9, U10: MCP96L00T-E/MX; QFN65P500X500X100-21N_MCP96L00T-E/MX

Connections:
3V3: C23.1, C24.1, C25.1, C26.1, C27.1, C28.1, R1.1, R9.1, R25.1, R31.1, R35.1, R39.1, U4.8 (VDD), U5.8 (VDD), U7.8 (VDD), U8.8 (VDD), U9.8 (VDD), U10.8 (VDD); also elsewhere on the board
GND: C23.2, C24.2, C25.2, C26.2, C27.2, C28.2, R3.1, R4.1, R26.1, R32.1, R36.1, R40.1, U4.1 (GND), U4.3 (GND), U4.5 (GND), U4.6 (GND), U4.7 (GND), U4.9 (GND), U4.10 (GND), U4.13 (GND), U4.17 (GND), U4.18 (GND), U4.21 (EXP), U4.22 (EXP), U4.23 (EXP), U4.24 (EXP), U4.25 (EXP), U4.26 (EXP), U4.27 (EXP), U4.28 (EXP), U4.29 (EXP), U4.30 (EXP), U5.1 (GND), U5.3 (GND), U5.5 (GND), U5.6 (GND), U5.7 (GND), U5.9 (GND), U5.10 (GND), U5.13 (GND), U5.17 (GND), U5.18 (GND), U5.21 (EXP), U5.22 (EXP), U5.23 (EXP), U5.24 (EXP), U5.25 (EXP), U5.26 (EXP), U5.27 (EXP), U5.28 (EXP), U5.29 (EXP), U5.30 (EXP), U7.1 (GND), U7.3 (GND), U7.5 (GND), U7.6 (GND), U7.7 (GND), U7.9 (GND), U7.10 (GND), U7.13 (GND), U7.17 (GND), U7.18 (GND), U7.21 (EXP), U7.22 (EXP), U7.23 (EXP), U7.24 (EXP), U7.25 (EXP), U7.26 (EXP), U7.27 (EXP), U7.28 (EXP), U7.29 (EXP), U7.30 (EXP), U8.1 (GND), U8.3 (GND), U8.5 (GND), U8.6 (GND), U8.7 (GND), U8.9 (GND), U8.10 (GND), U8.13 (GND), U8.17 (GND), U8.18 (GND), U8.21 (EXP), U8.22 (EXP), U8.23 (EXP), U8.24 (EXP), U8.25 (EXP), U8.26 (EXP), U8.27 (EXP), U8.28 (EXP), U8.29 (EXP), U8.30 (EXP), U9.1 (GND), U9.3 (GND), U9.5 (GND), U9.6 (GND), U9.7 (GND), U9.9 (GND), U9.10 (GND), U9.13 (GND), U9.17 (GND), U9.18 (GND), U9.21 (EXP), U9.22 (EXP), U9.23 (EXP), U9.24 (EXP), U9.25 (EXP), U9.26 (EXP), U9.27 (EXP), U9.28 (EXP), U9.29 (EXP), U9.30 (EXP), U10.1 (GND), U10.3 (GND), U10.5 (GND), U10.6 (GND), U10.7 (GND), U10.9 (GND), U10.10 (GND), U10.13 (GND), U10.17 (GND), U10.18 (GND), U10.21 (EXP), U10.22 (EXP), U10.23 (EXP), U10.24 (EXP), U10.25 (EXP), U10.26 (EXP), U10.27 (EXP), U10.28 (EXP), U10.29 (EXP), U10.30 (EXP); also elsewhere on the board
unnamed: H7.B2,8, R17.1
unnamed: H8.B2,8, R18.1
unnamed: R1.2, R3.2, U8.16 (ADDR)
unnamed: R4.2, R9.2, U7.16 (ADDR)
unnamed: H9.B2,8, R13.1
unnamed: H10.B2,8, R14.1
unnamed: H11.B2,8, R20.1
unnamed: H12.B2,8, R19.1
unnamed: H13.B2,8, R22.1
unnamed: H14.B2,8, R21.1
unnamed: H15.B2,8, R23.1
unnamed: H16.B2,8, R24.1
unnamed: H17.B2,8, R15.1
unnamed: H18.B2,8, R16.1
unnamed: C10.1, R13.2, U4.2 (VIN+)
unnamed: C10.2, R14.2, U4.4 (VIN-)
unnamed: C12.1, R20.2, U7.2 (VIN+)
unnamed: C12.2, R19.2, U7.4 (VIN-)
unnamed: C15.1, R23.2, U8.2 (VIN+)
unnamed: C1.2, R21.2, U10.4 (VIN-)
unnamed: C15.2, R24.2, U8.4 (VIN-)
unnamed: C1.1, R22.2, U10.2 (VIN+)
unnamed: C13.1, R17.2, U9.2 (VIN+)
unnamed: C13.2, R18.2, U9.4 (VIN-)
unnamed: C11.1, R15.2, U5.2 (VIN+)
unnamed: C11.2, R16.2, U5.4 (VIN-)
unnamed: R25.2, R26.2, U5.16 (ADDR)
unnamed: R31.2, R32.2, U9.16 (ADDR)
unnamed: R35.2, R36.2, U4.16 (ADDR)
unnamed: R39.2, R40.2, U10.16 (ADDR)
SCL: U4.19 (SCL), U5.19 (SCL), U7.19 (SCL), U8.19 (SCL), U9.19 (SCL), U10.19 (SCL); also elsewhere on the board
SDA: U4.20 (SDA), U5.20 (SDA), U7.20 (SDA), U8.20 (SDA), U9.20 (SDA), U10.20 (SDA); also elsewhere on the board

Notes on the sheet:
TC to Digital ADDR=0x60
TC to Digital ADDR=0x61
TC to Digital ADDR=0x62
TC to Digital ADDR=0x67
TC to Digital ADDR=0x63
TC to Digital ADDR=0x64
amtpsfta-tc-breakout-01

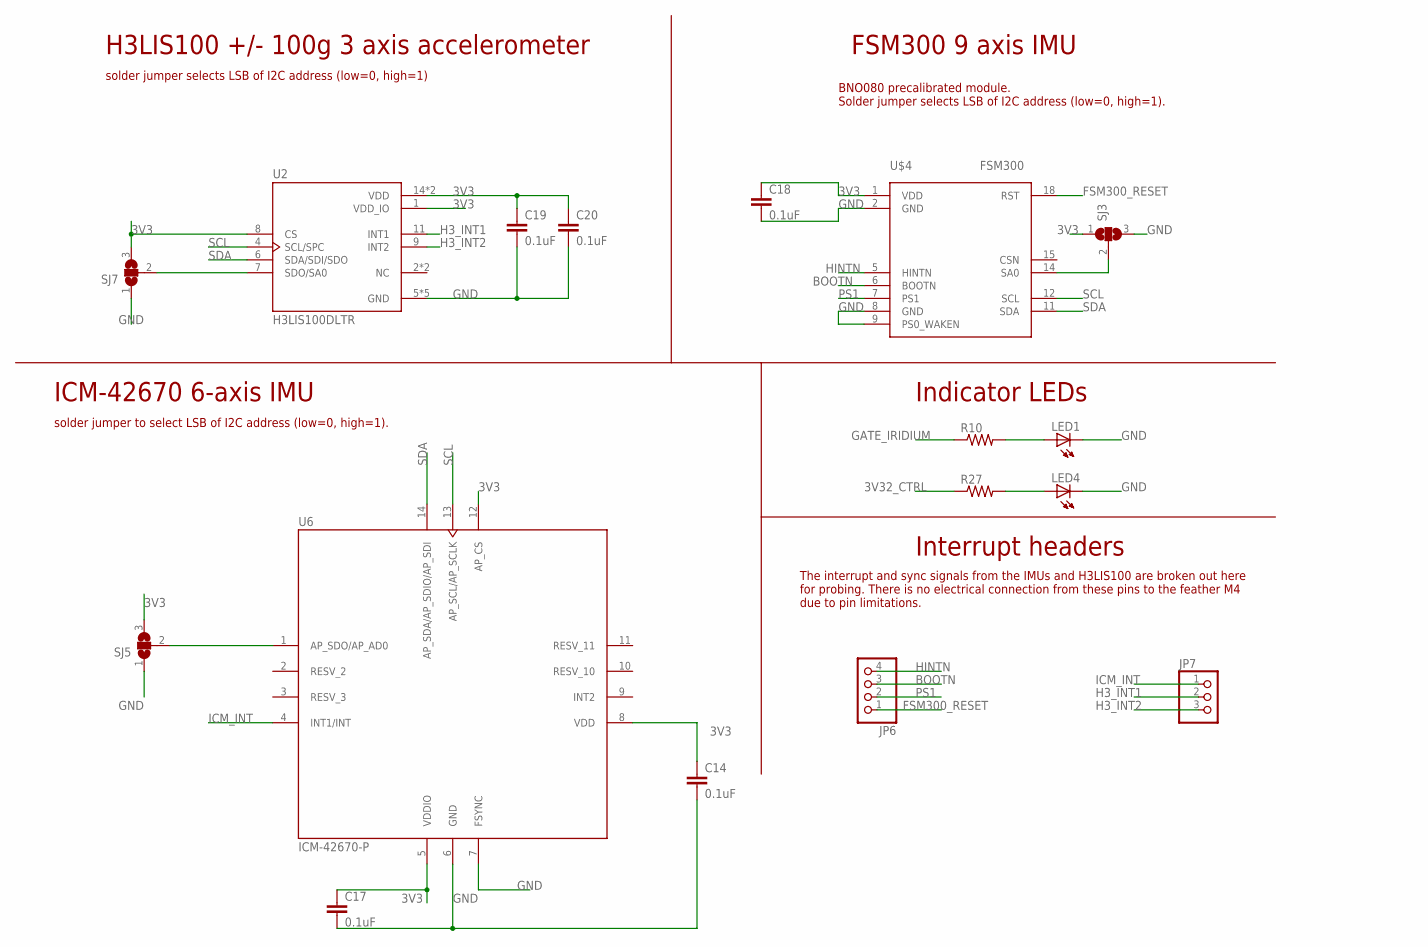
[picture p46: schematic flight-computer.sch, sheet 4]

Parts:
C14, C17, C18, C19, C20: 0.1uF; C0603
JP6: PINHD-1X4; 1X04
JP7: PINHD-1X3; 1X03
LED1, LED4: LEDCHIPLED_0603; CHIPLED_0603
R10, R27: R-US_R0603; R0603
SJ3, SJ5, SJ7: SJ2W; SJ_2
U2: H3LIS100DLTR; PQFN50P300X300X100-16N
U6: ICM-42670-P; IC_ICM-42670-P
U$4: FSM300; FSM300_FOOTPRINT

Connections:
3V3: C14.1, C17.1, C18.1, C19.1, C20.1, SJ3.1, SJ5.3, SJ7.3, U2.1 (VDD_IO), U2.8 (CS), U2.14 (VDD), U2.15 (VDD), U6.5 (VDDIO), U6.8 (VDD), U6.12 (AP_CS), U$4.1 (VDD); also elsewhere on the board
3V32_CTRL: R27.1; also elsewhere on the board
BOOTN: JP6.3, U$4.6 (BOOTN)
FSM300_RESET: JP6.1, U$4.18 (RST)
GATE_IRIDIUM: R10.1; also elsewhere on the board
GND: C14.2, C17.2, C18.2, C19.2, C20.2, LED1.C, LED4.C, SJ3.3, SJ5.1, SJ7.1, U2.5 (GND), U2.10 (GND), U2.12 (GND), U2.13 (GND), U2.16 (GND), U6.6 (GND), U6.7 (FSYNC), U$4.2 (GND), U$4.8 (GND), U$4.9 (PS0_WAKEN); also elsewhere on the board
H3_INT1: JP7.2, U2.11 (INT1)
H3_INT2: JP7.3, U2.9 (INT2)
HINTN: JP6.4, U$4.5 (HINTN)
ICM_INT: JP7.1, U6.4 (INT1/INT)
unnamed: SJ5.2, U6.1 (AP_SDO/AP_AD0)
unnamed: LED1.A, R10.2
unnamed: SJ7.2, U2.7 (SDO/SA0)
unnamed: LED4.A, R27.2
unnamed: SJ3.2, U$4.14 (SA0)
PS1: JP6.2, U$4.7 (PS1)
SCL: U2.4 (SCL/SPC), U6.13 (AP_SCL/AP_SCLK), U$4.12 (SCL); also elsewhere on the board
SDA: U2.6 (SDA/SDI/SDO), U6.14 (AP_SDA/AP_SDIO/AP_SDI), U$4.11 (SDA); also elsewhere on the board

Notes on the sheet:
FSM300 9 axis IMU
BNO080 precalibrated module. Solder jumper selects LSB of I2C address (low=0, high=1).
H3LIS100 +/- 100g 3 axis accelerometer
solder jumper selects LSB of I2C address (low=0, high=1)
ICM-42670 6-axis IMU
solder jumper to select LSB of I2C address (low=0, high=1).
Indicator LEDs
Interrupt headers
The interrupt and sync signals from the IMUs and H3LIS100 are broken out here for probing. There is no electrical connection from these pins to the feather M4 due to pin limitations.

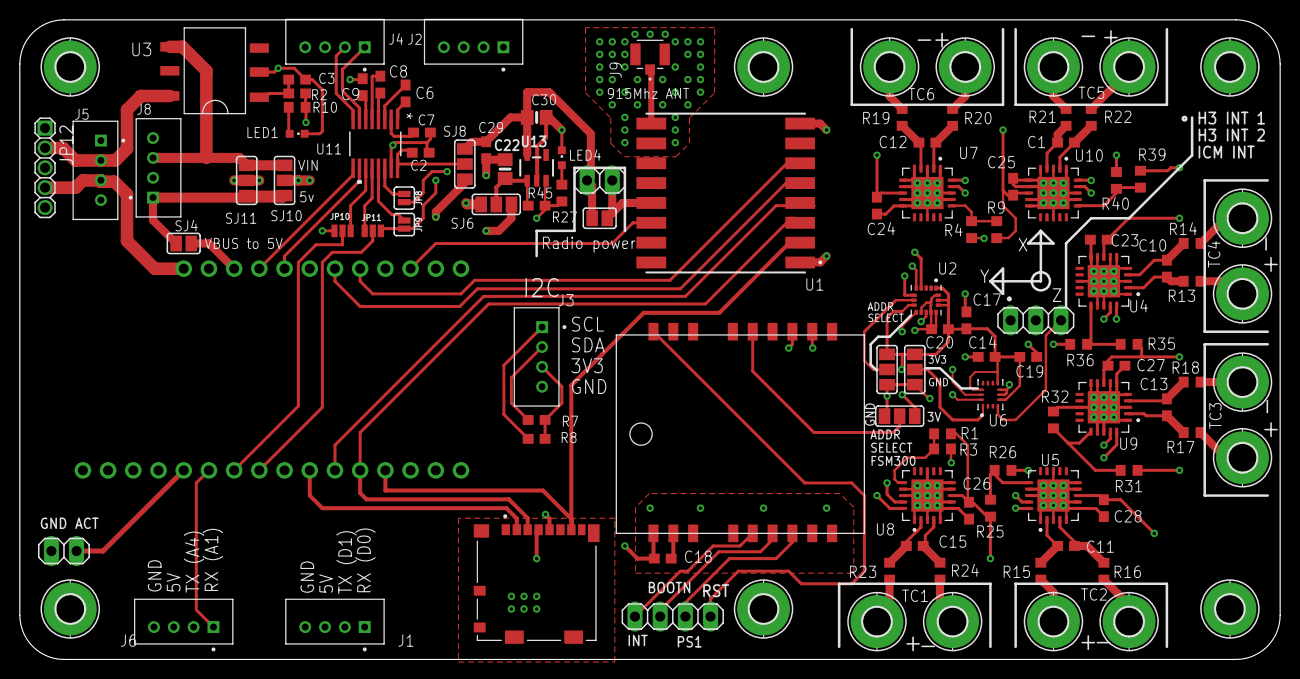
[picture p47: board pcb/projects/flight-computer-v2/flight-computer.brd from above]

Board: 4 copper layers, 127.0 x 64.4 mm, 118 parts (0 on the bottom side), 91 nets.

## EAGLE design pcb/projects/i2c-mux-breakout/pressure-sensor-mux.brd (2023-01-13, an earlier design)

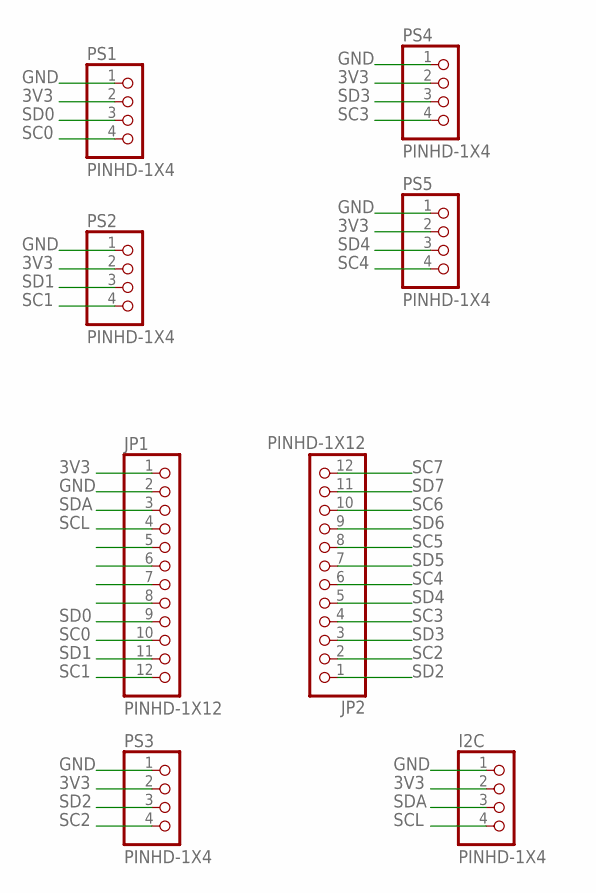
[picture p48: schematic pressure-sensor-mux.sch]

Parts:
I2C: PINHD-1X4; 1X04
JP1, JP2: PINHD-1X12; 1X12
PS1, PS2, PS3, PS4, PS5: PINHD-1X4; 1X04

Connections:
3V3: I2C.2, JP1.1, PS1.2, PS2.2, PS3.2, PS4.2, PS5.2
GND: I2C.1, JP1.2, PS1.1, PS2.1, PS3.1, PS4.1, PS5.1
SC0: JP1.10, PS1.4
SC1: JP1.12, PS2.4
SC2: JP2.2, PS3.4
SC3: JP2.4, PS4.4
SC4: JP2.6, PS5.4
SC5: JP2.8
SC6: JP2.10
SC7: JP2.12
SCL: I2C.4, JP1.4
SD0: JP1.9, PS1.3
SD1: JP1.11, PS2.3
SD2: JP2.1, PS3.3
SD3: JP2.3, PS4.3
SD4: JP2.5, PS5.3
SD5: JP2.7
SD6: JP2.9
SD7: JP2.11
SDA: I2C.3, JP1.3

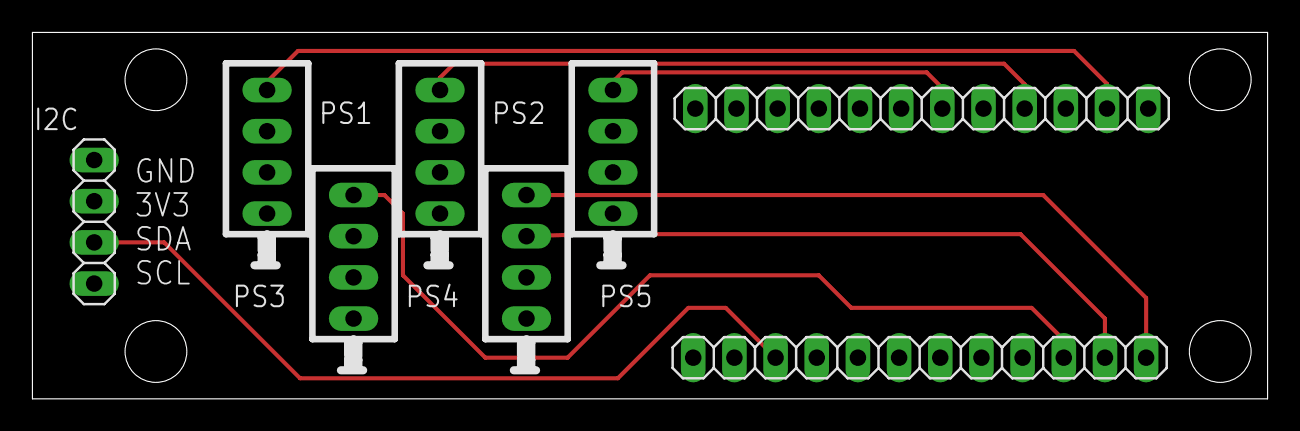
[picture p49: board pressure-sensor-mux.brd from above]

Board: 4 copper layers, 76.2 x 22.6 mm, 8 parts (0 on the bottom side), 14 nets.

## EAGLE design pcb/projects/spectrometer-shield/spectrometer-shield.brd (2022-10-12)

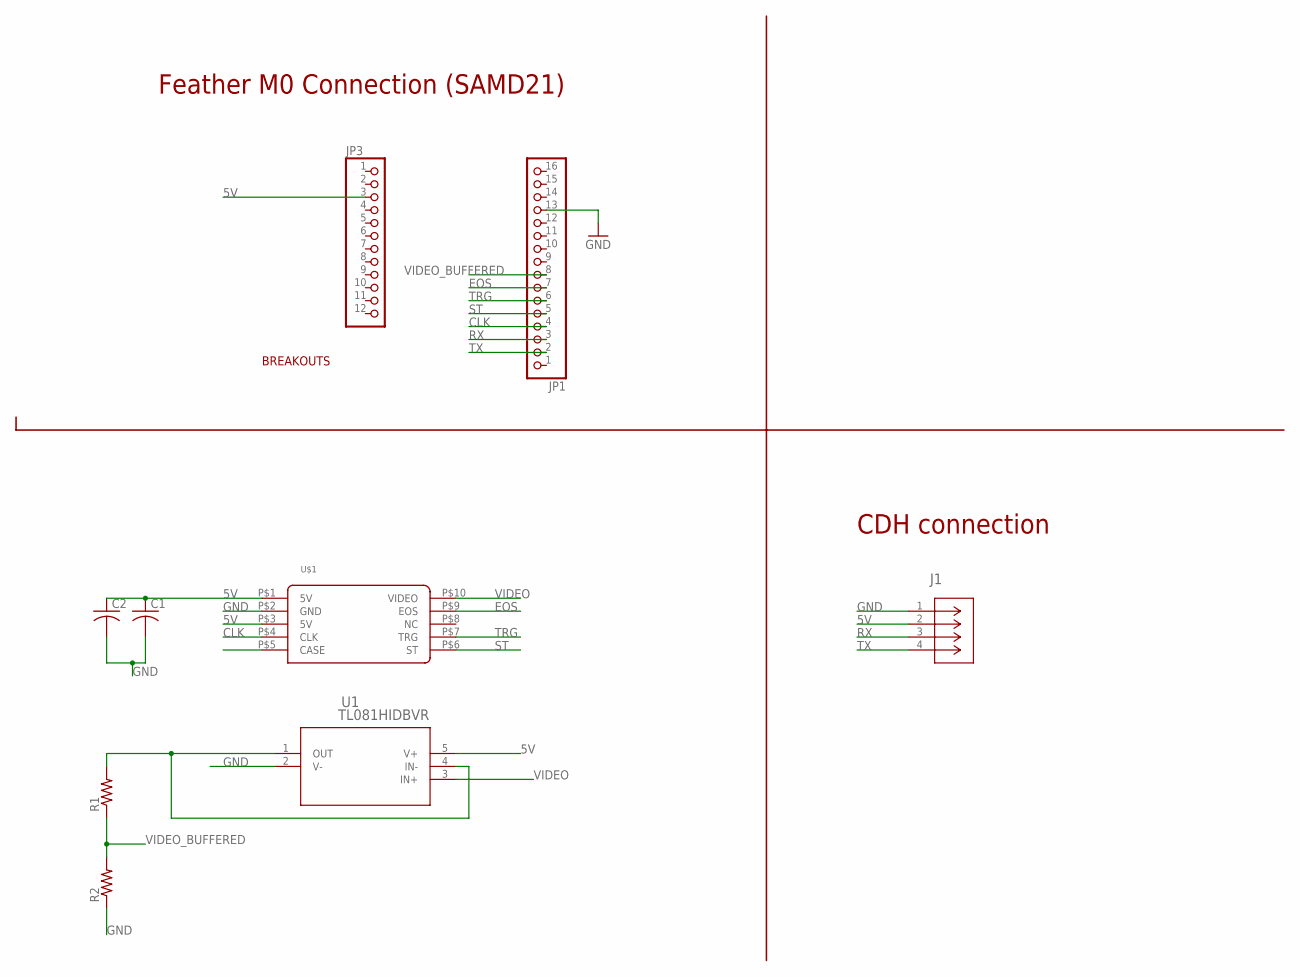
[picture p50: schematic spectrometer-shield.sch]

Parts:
C1: C-USC1206; C1206
C2: C-USC0603; C0603
J1: S4B-PH-SM4-TB(LF)(SN); CONN_S4B-PH-SM4-TB(LF)(SN)_JST
JP1: HEADER-1X16ROUND; 1X16_ROUND
JP3: HEADER-1X12; 1X12_ROUND
R1, R2: R-US_R0603; R0603
U1: TL081HIDBVR; SOT-23-5_DBV_TEX
U$1: C12880MA; C12880MA_FOOTPRINT

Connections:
5V: C1.1, C2.1, J1.2, JP3.3, U1.5 (V+), U$1.P$1 (5V), U$1.P$3 (5V)
CLK: JP1.4, U$1.P$4 (CLK)
EOS: JP1.7, U$1.P$9 (EOS)
GND: C1.2, C2.2, J1.1, JP1.13, R2.1, U1.2 (V-), U$1.P$2 (GND), U$1.P$5 (CASE)
unnamed: R1.2, U1.1 (OUT), U1.4 (IN-)
RX: J1.3, JP1.3
ST: JP1.5, U$1.P$6 (ST)
TRG: JP1.6, U$1.P$7 (TRG)
TX: J1.4, JP1.2
VIDEO: U1.3 (IN+), U$1.P$10 (VIDEO)
VIDEO_BUFFERED: JP1.8, R1.1, R2.2

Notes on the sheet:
BREAKOUTS
CDH connection
Feather M0 Connection (SAMD21)

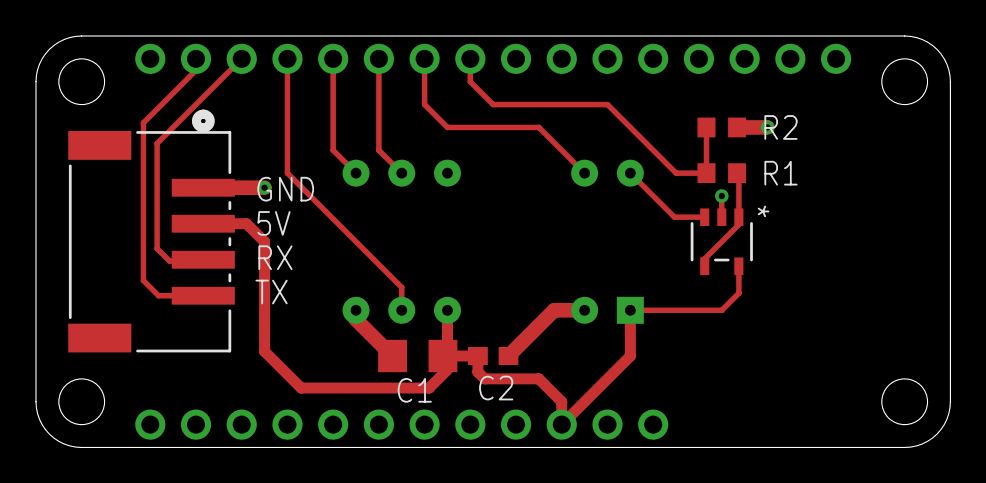
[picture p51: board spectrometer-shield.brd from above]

Board: 2 copper layers, 50.8 x 22.9 mm, 9 parts (1 on the bottom side), 11 nets.

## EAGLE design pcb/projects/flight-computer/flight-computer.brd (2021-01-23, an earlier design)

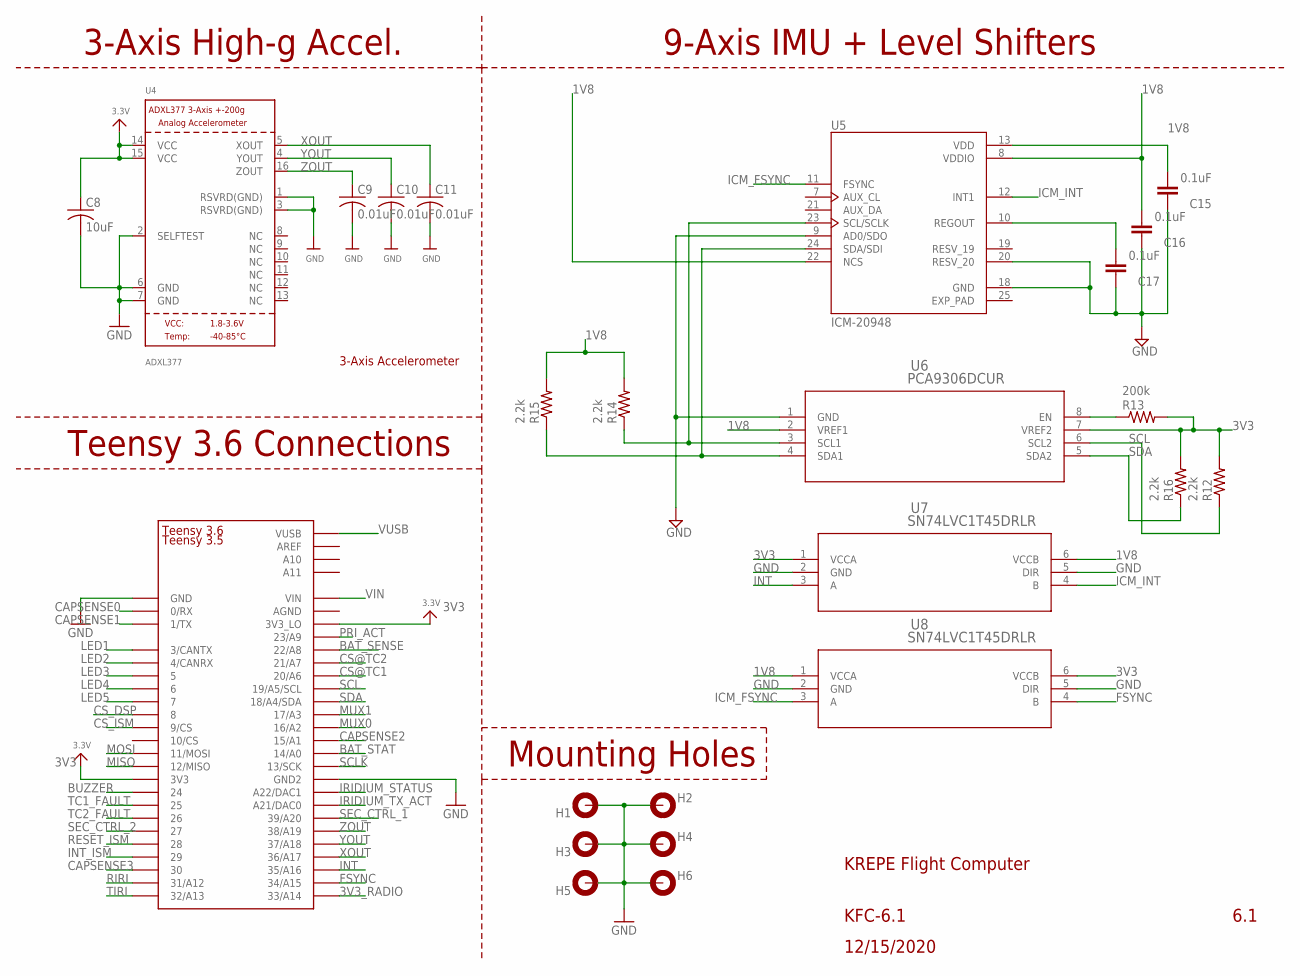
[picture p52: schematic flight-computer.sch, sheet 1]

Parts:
C8: 10uF; C0603
C9, C10, C11: 0.01uF; C0603
C15, C16, C17: 0.1uF; C0603
H1, H2, H3, H4, H5, H6: MOUNT-PAD-ROUND2.8; 2,8-PAD
R12, R14, R15, R16: 2.2k; R0603
R13: 200k; R0603
U4: ADXL377; LFCSP16_LQ
U5: ICM-20948; QFN40P300X300X105-25N
U6: PCA9306DCUR; DCU8
U7, U8: SN74LVC1T45DRLR; DRL6
U$1: TEENSY_3.5/3.6_BASIC

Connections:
1V8: C15.2, C16.2, R14.2, R15.2, U5.8 (VDDIO), U5.13 (VDD), U5.22 (NCS), U6.2 (VREF1), U7.6 (VCCB), U8.1 (VCCA); also elsewhere on the board
3V3: C8.1, R12.2, R13.2, R16.2, U4.14 (VCC), U4.15 (VCC), U6.7 (VREF2), U7.1 (VCCA), U8.6 (VCCB), U$1.3V3, U$1.3V3_LO; also elsewhere on the board
3V3_RADIO: U$1.33/A14; also elsewhere on the board
BAT_SENSE: U$1.22/A8; also elsewhere on the board
BAT_STAT: U$1.14/A0; also elsewhere on the board
BUZZER: U$1.24; also elsewhere on the board
CAPSENSE0: U$1.0/RX; also elsewhere on the board
CAPSENSE1: U$1.1/TX; also elsewhere on the board
CAPSENSE2: U$1.15/A1; also elsewhere on the board
CAPSENSE3: U$1.30; also elsewhere on the board
CS@TC1: U$1.20/A6; also elsewhere on the board
CS@TC2: U$1.21/A7; also elsewhere on the board
CS_DSP: U$1.8; also elsewhere on the board
CS_ISM: U$1.9/CS; also elsewhere on the board
EXP_PAD: U5.25 (EXP_PAD)
FSYNC: U8.4 (B), U$1.34/A15
GND: C8.2, C9.2, C10.2, C11.2, C15.1, C16.1, C17.1, H1.B2,8, H2.B2,8, H3.B2,8, H4.B2,8, H5.B2,8, H6.B2,8, U4.1 (RSVRD(GND)), U4.2 (SELFTEST), U4.3 (RSVRD(GND)), U4.6 (GND), U4.7 (GND), U5.9 (AD0/SDO), U5.18 (GND), U5.20 (RESV_20), U6.1 (GND), U7.2 (GND), U7.5 (DIR), U8.2 (GND), U8.5 (DIR), U$1.GND; also elsewhere on the board
ICM_FSYNC: U5.11 (FSYNC), U8.3 (A)
ICM_INT: U5.12 (INT1), U7.4 (B)
INT: U7.3 (A), U$1.35/A16
INT_ISM: U$1.29; also elsewhere on the board
IRIDIUM_STATUS: U$1.A22/DAC1; also elsewhere on the board
IRIDIUM_TX_ACT: U$1.21/DAC0 (A21/DAC0); also elsewhere on the board
LED1: U$1.3/CANTX; also elsewhere on the board
LED2: U$1.4/CANRX; also elsewhere on the board
LED3: U$1.5; also elsewhere on the board
LED4: U$1.6; also elsewhere on the board
LED5: U$1.7; also elsewhere on the board
MISO: U$1.12/MISO; also elsewhere on the board
MOSI: U$1.11/MOSI; also elsewhere on the board
MUX0: U$1.16/A2; also elsewhere on the board
MUX1: U$1.17/A3; also elsewhere on the board
unnamed: R13.1, U6.8 (EN)
unnamed: C17.2, U5.10 (REGOUT)
unnamed: R14.1, U5.23 (SCL/SCLK), U6.3 (SCL1)
unnamed: R15.1, U5.24 (SDA/SDI), U6.4 (SDA1)
PRI_ACT: U$1.23/A9; also elsewhere on the board
RESET_ISM: U$1.28; also elsewhere on the board
RIRI: U$1.31/A12; also elsewhere on the board
SCL: R12.1, U6.6 (SCL2), U$1.19/A5/SCL
SCLK: U$1.13/SCK; also elsewhere on the board
SDA: R16.1, U6.5 (SDA2), U$1.18/A4/SDA
SEC_CTRL_1: U$1.39/A20; also elsewhere on the board
SEC_CTRL_2: U$1.27; also elsewhere on the board
TC1_FAULT: U$1.25; also elsewhere on the board
TC2_FAULT: U$1.26; also elsewhere on the board
TIRI: U$1.32/A13; also elsewhere on the board
VIN: U$1.VIN; also elsewhere on the board
VUSB: U$1.VUSB; also elsewhere on the board
XOUT: C11.1, U4.5 (XOUT), U$1.36/A17
YOUT: C10.1, U4.4 (YOUT), U$1.37/A18
ZOUT: C9.1, U4.16 (ZOUT), U$1.38/A19

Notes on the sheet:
3-Axis Accelerometer
Teensy 3.5
9-Axis IMU + Level Shifters
Teensy 3.6 Connections
3-Axis High-g Accel.
Mounting Holes
KREPE Flight Computer
6.1
KFC-6.1
12/15/2020

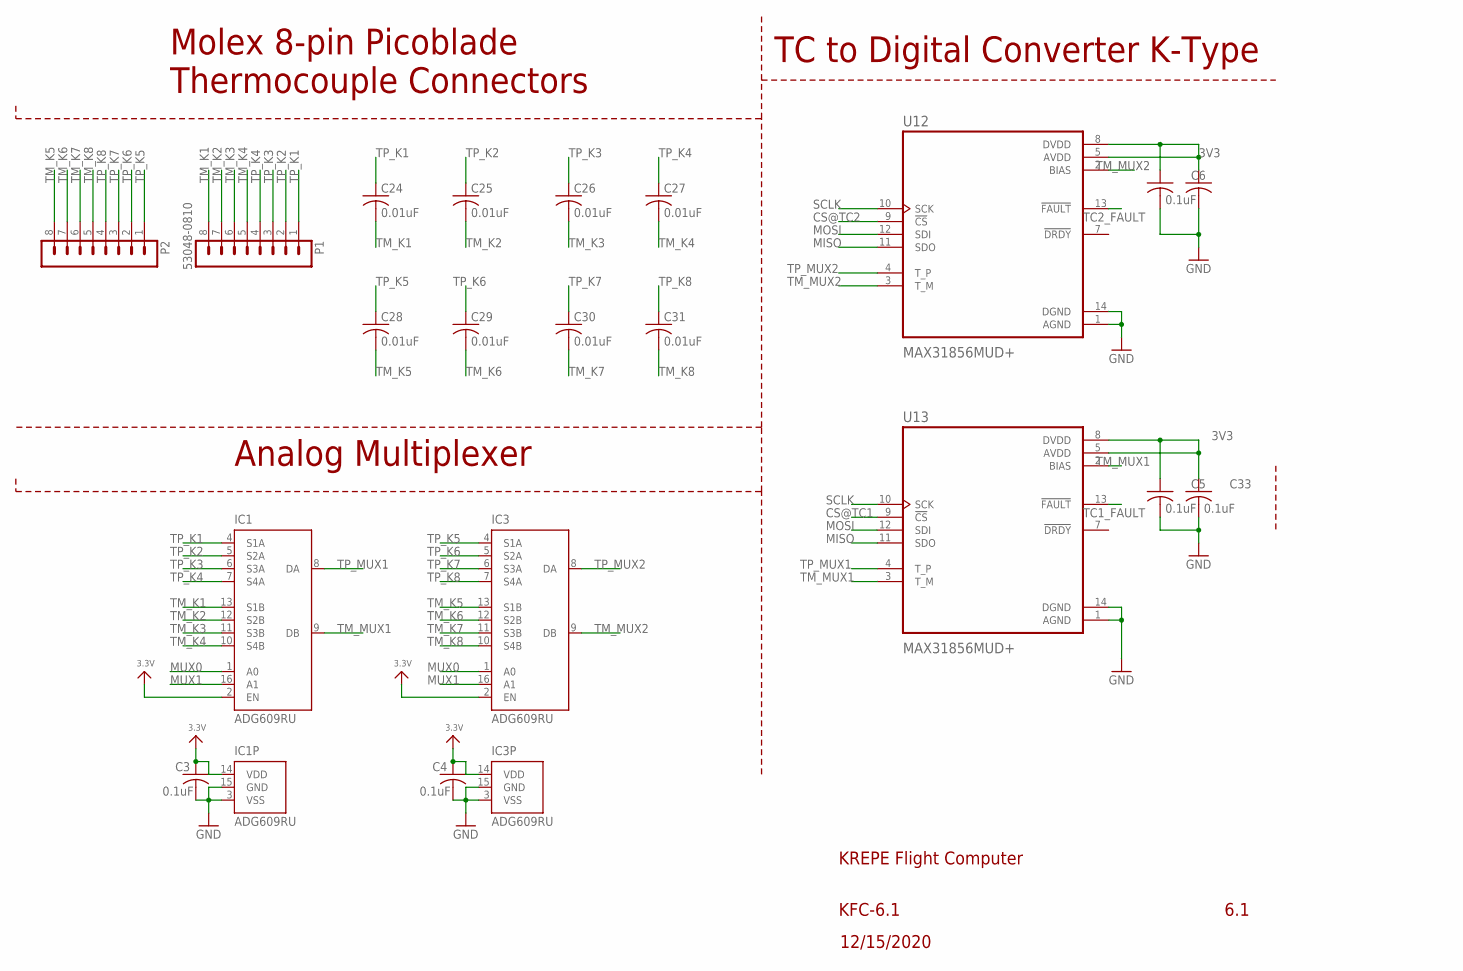
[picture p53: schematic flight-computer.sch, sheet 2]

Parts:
C3, C4, C5, C6, C32, C33: 0.1uF; C0603
C24, C25, C26, C27, C28, C29, C30, C31: 0.01uF; C0603
IC1, IC3: ADG609RU; TSSOP16
P1, P2: 53048-0810
U12, U13: MAX31856MUD+; SOP65P640X110-14N

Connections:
3V3: C3.1, C4.1, C5.1, C6.1, C32.1, C33.1, IC1.2 (EN), IC1.14 (VDD), IC3.2 (EN), IC3.14 (VDD), U12.5 (AVDD), U12.8 (DVDD), U13.5 (AVDD), U13.8 (DVDD); also elsewhere on the board
CS@TC1: U13.9 (!CS); also elsewhere on the board
CS@TC2: U12.9 (!CS); also elsewhere on the board
GND: C3.2, C4.2, C5.2, C6.2, C32.2, C33.2, IC1.3 (VSS), IC1.15 (GND), IC3.3 (VSS), IC3.15 (GND), U12.1 (AGND), U12.14 (DGND), U13.1 (AGND), U13.14 (DGND); also elsewhere on the board
MISO: U12.11 (SDO), U13.11 (SDO); also elsewhere on the board
MOSI: U12.12 (SDI), U13.12 (SDI); also elsewhere on the board
MUX0: IC1.1 (A0), IC3.1 (A0); also elsewhere on the board
MUX1: IC1.16 (A1), IC3.16 (A1); also elsewhere on the board
SCLK: U12.10 (SCK), U13.10 (SCK); also elsewhere on the board
TC1_FAULT: U13.13 (!FAULT); also elsewhere on the board
TC2_FAULT: U12.13 (!FAULT); also elsewhere on the board
TM_K1: C24.2, IC1.13 (S1B), P1.8
TM_K2: C25.2, IC1.12 (S2B), P1.7
TM_K3: C26.2, IC1.11 (S3B), P1.6
TM_K4: C27.2, IC1.10 (S4B), P1.5
TM_K5: C28.2, IC3.13 (S1B), P2.8
TM_K6: C29.2, IC3.12 (S2B), P2.7
TM_K7: C30.2, IC3.11 (S3B), P2.6
TM_K8: C31.2, IC3.10 (S4B), P2.5
TM_MUX1: IC1.9 (DB), U13.2 (BIAS), U13.3 (T_M)
TM_MUX2: IC3.9 (DB), U12.2 (BIAS), U12.3 (T_M)
TP_K1: C24.1, IC1.4 (S1A), P1.1
TP_K2: C25.1, IC1.5 (S2A), P1.2
TP_K3: C26.1, IC1.6 (S3A), P1.3
TP_K4: C27.1, IC1.7 (S4A), P1.4
TP_K5: C28.1, IC3.4 (S1A), P2.1
TP_K6: C29.1, IC3.5 (S2A), P2.2
TP_K7: C30.1, IC3.6 (S3A), P2.3
TP_K8: C31.1, IC3.7 (S4A), P2.4
TP_MUX1: IC1.8 (DA), U13.4 (T_P)
TP_MUX2: IC3.8 (DA), U12.4 (T_P)

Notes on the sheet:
Analog Multiplexer
TC to Digital Converter K-Type
Molex 8-pin Picoblade Thermocouple Connectors
6.1
KFC-6.1
12/15/2020
KREPE Flight Computer

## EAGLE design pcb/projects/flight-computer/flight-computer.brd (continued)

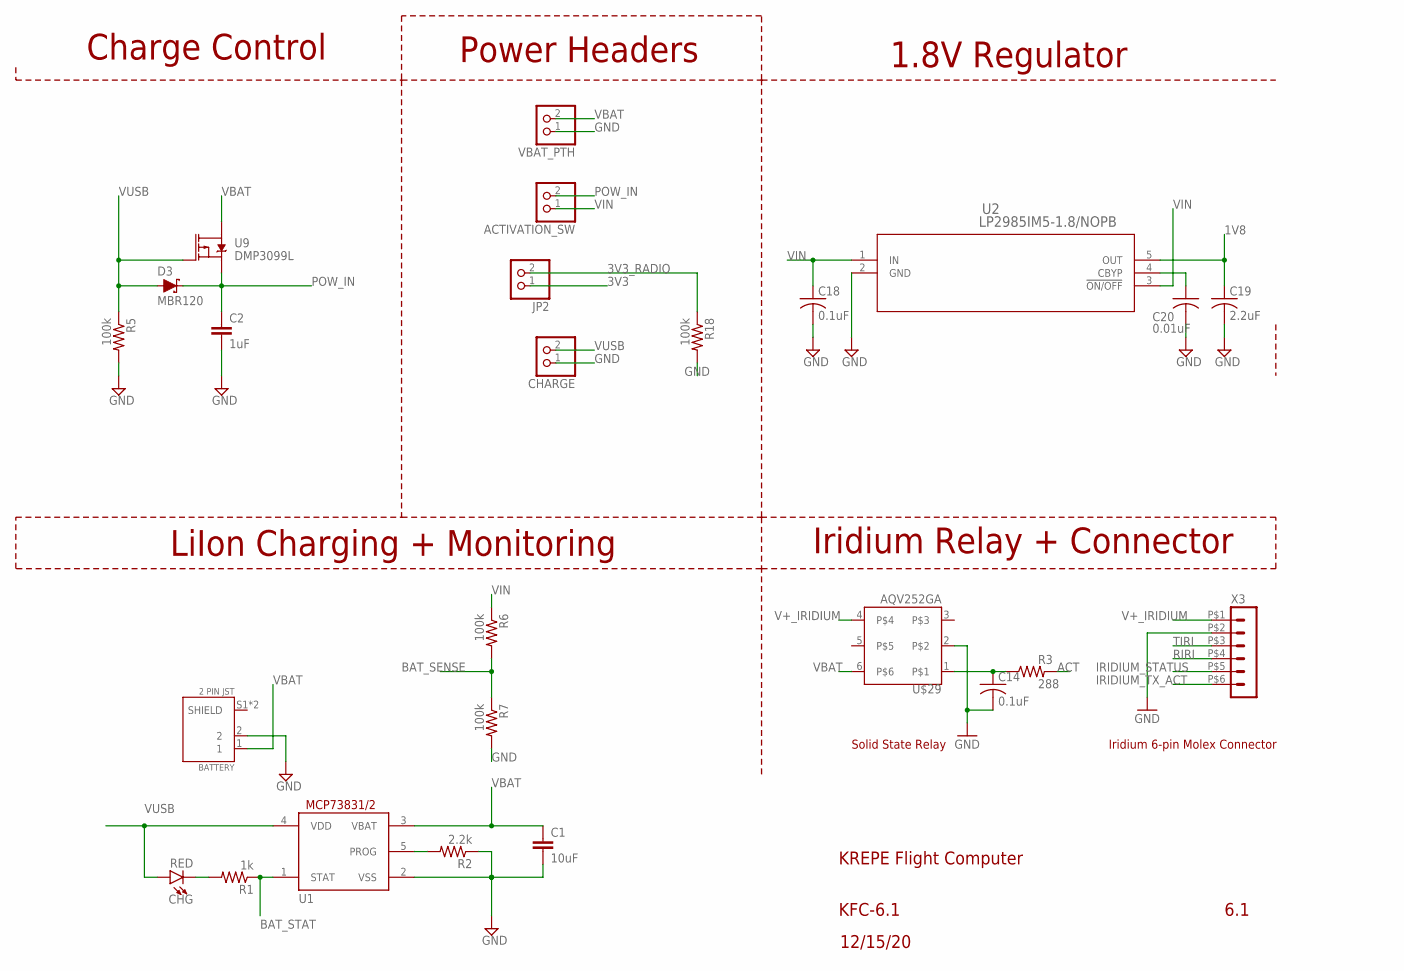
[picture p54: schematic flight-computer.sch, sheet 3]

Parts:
ACTIVATION_SW: PINHD-1X2; 1X02
BATTERY: 2 PIN JST; JST_S2B-PH-SM4-TB(LF)(SN)
C1: 10uF; C0603
C2: 1uF; C0603
C14, C18: 0.1uF; C0603
C19: 2.2uF; C0603
C20: 0.01uF; C0603
CHARGE: PINHD-1X2; 1X02
CHG: RED; LED-0603
D3: MBR120; SOD123FL
JP2: PINHD-1X2; 1X02
R1: 1k; R0603
R2: 2.2k; R0603
R3: 288; R0603
R5, R6, R7, R18: 100k; R0603
U1: MCP73831/OT; SOT23-5L
U2: LP2985IM5-1.8/NOPB; MF05A
U9: DMP3099L; SOT23
U$29: AQV252GA; DIP6
VBAT_PTH: PINHD-1X2; 1X02
X3: HEADER_POS6_43650-0600; 43650-0600

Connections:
1V8: C19.1, U2.5 (OUT); also elsewhere on the board
3V3: JP2.1; also elsewhere on the board
3V3_RADIO: JP2.2, R18.1; also elsewhere on the board
ACT: R3.2; also elsewhere on the board
BAT_SENSE: R6.2, R7.1; also elsewhere on the board
BAT_STAT: R1.1, U1.1 (STAT); also elsewhere on the board
GND: BATTERY.2, C1.2, C2.2, C14.2, C18.2, C19.2, C20.2, CHARGE.1, R2.1, R5.2, R7.2, R18.2, U1.2 (VSS), U2.2 (GND), U$29.2, VBAT_PTH.1, X3.P$2 (2); also elsewhere on the board
IRIDIUM_STATUS: X3.P$5 (5); also elsewhere on the board
IRIDIUM_TX_ACT: X3.P$6 (6); also elsewhere on the board
unnamed: R2.2, U1.5 (PROG)
unnamed: C14.1, R3.1, U$29.1
unnamed: CHG.C, R1.2
unnamed: C20.1, U2.4 (CBYP)
POW_IN: ACTIVATION_SW.2, C2.1, D3.C, U9.2 (S)
RIRI: X3.P$4 (4); also elsewhere on the board
TIRI: X3.P$3 (3); also elsewhere on the board
V+_IRIDIUM: U$29.4, X3.P$1 (1)
VBAT: BATTERY.1, C1.1, U1.3 (VBAT), U9.3 (D), U$29.6, VBAT_PTH.2
VIN: ACTIVATION_SW.1, C18.1, R6.1, U2.1 (IN), U2.3 (!ON/OFF); also elsewhere on the board
VUSB: CHARGE.2, CHG.A, D3.A, R5.1, U1.4 (VDD), U9.1 (G); also elsewhere on the board

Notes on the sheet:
Iridium 6-pin Molex Connector
Solid State Relay
Iridium Relay + Connector
Charge Control
Power Headers
LiIon Charging + Monitoring
1.8V Regulator
6.1
KFC-6.1
12/15/20
KREPE Flight Computer


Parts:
ANT: U.FL-R-SMT-1(10); CONN_R-SMT-1(10)
C12, C13: 0.1uF; C0603
C22: 1uF; C0603
CAPSENSE: 53048-0810
JP3: PINHD-1X2; 1X02
LED1, LED2, LED3, LED4, LED5: LEDCHIP-LED0603; CHIP-LED0603
R4, R8, R9, R10, R11: 470; R0603
R19: 100; R0603
U3: COM-13909; MOD_COM-13909
U11: DPS310XTSA1; XDCR_DPS310XTSA1

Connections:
3V3: C12.1, C13.1, U11.6 (VDDIO), U11.8 (VDD); also elsewhere on the board
3V3_RADIO: C22.1, U3.13 (3.3V); also elsewhere on the board
BUZZER: JP3.1; also elsewhere on the board
CAPSENSE0: CAPSENSE.4; also elsewhere on the board
CAPSENSE1: CAPSENSE.2; also elsewhere on the board
CAPSENSE2: CAPSENSE.6; also elsewhere on the board
CAPSENSE3: CAPSENSE.8; also elsewhere on the board
CS_DSP: U11.2 (!CSB); also elsewhere on the board
CS_ISM: U3.5 (NSS); also elsewhere on the board
GND: ANT.2, ANT.3, C12.2, C13.2, C22.2, CAPSENSE.1, CAPSENSE.3, CAPSENSE.5, CAPSENSE.7, LED1.C, LED2.C, LED3.C, LED4.C, LED5.C, R19.1, U3.1 (GND), U3.8 (GND), U3.10 (GND), U11.1 (GND), U11.7 (GND); also elsewhere on the board
INT_ISM: U3.14 (DIO0); also elsewhere on the board
LED1: R4.1; also elsewhere on the board
LED2: R8.1; also elsewhere on the board
LED3: R9.1; also elsewhere on the board
LED4: R10.1; also elsewhere on the board
LED5: R11.1; also elsewhere on the board
MISO: U3.2 (MISO), U11.5 (SDO); also elsewhere on the board
MOSI: U3.3 (MOSI), U11.3 (SDI); also elsewhere on the board
unnamed: JP3.2, R19.2
unnamed: ANT.1, U3.9 (ANT)
unnamed: LED1.A, R4.2
unnamed: LED2.A, R8.2
unnamed: LED3.A, R9.2
unnamed: LED4.A, R10.2
unnamed: LED5.A, R11.2
RESET_ISM: U3.6 (RESET); also elsewhere on the board
SCLK: U3.4 (SCK), U11.4 (SCK); also elsewhere on the board

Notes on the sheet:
ISM Radio
6.1
Status LEDs
Capacitive Sense Header
Buzzer Header
Barometric Pressure Sensor
KFC-6.1
KREPE Flight Computer


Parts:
C7: 1uF; 0603-NO
CN1: 4U#20329; 4UCONN_20329_V2
IC2: ATSAMD21E; QFN32_5MM
JP1: PINHD-1X4; 1X04
R17: 10k; R0603
SJ1: SJ
U10: SN74LVC1G08DCKR; SOT65P210X110-5N

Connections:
3V3: IC2.9 (VDDA), IC2.30 (VDDIN), U10.5 (VCC); also elsewhere on the board
!RESET: IC2.26 (/RESET), JP1.3
ACT: U10.4 (Y); also elsewhere on the board
CS@TC1: IC2.3 (PA02/EINT2/AIN0/Y0/VOUT); also elsewhere on the board
CS@TC2: IC2.13 (PA10/I10/AIN18/SERCOM0+2.2/I2SCK); also elsewhere on the board
D+: CN1.D+, IC2.24 (PA25/I13/SERCOM3+5.3/D+)
D-: CN1.D-, IC2.23 (PA24/I12/SERCOM3+5.2/D-)
GND: C7.2, CN1.BASE@1 (GND), CN1.BASE@2 (GND), CN1.GND, CN1.SPRT@1 (GND), CN1.SPRT@2 (GND), CN1.SPRT@3 (GND), CN1.SPRT@4 (GND), IC2.10 (GND), IC2.28 (GNDA), IC2.33 (GND), JP1.4, R17.2, U10.3 (GND); also elsewhere on the board
MISO: IC2.12 (PA09/I2C/I9/AIN17/SERCOM0+2.1/I2SMC); also elsewhere on the board
MOSI: IC2.7 (PA06/EINT6/AIN6/SERCOM0.2); also elsewhere on the board
MUX0: IC2.18 (PA17/I2C/I1/SERCOM1+3.1); also elsewhere on the board
MUX1: IC2.19 (PA18/I2/SERCOM1+3.2); also elsewhere on the board
PRI_ACT: SJ1.1, U10.1 (A); also elsewhere on the board
SCLK: IC2.8 (PA07/I7/AIN7/SERCOM0.3/I2SD0); also elsewhere on the board
SEC_ACT: IC2.1 (PA00/EINT0/SERCOM1.0), SJ1.2, U10.2 (B)
SEC_CTRL_1: IC2.2 (PA01/EINT1/SERCOM1.1), R17.1; also elsewhere on the board
SEC_CTRL_2: IC2.11 (PA08/I2C/AIN16/SERCOM0+2.0/I2SD1); also elsewhere on the board
SWCLK: IC2.31 (PA30/I10/SECOM1.2/SWCLK), JP1.2
SWDIO: IC2.32 (PA31/I11/SECOM1.3/SWDIO), JP1.1
TC1_FAULT: IC2.15 (PA14/I14/SERCOM2+4.2); also elsewhere on the board
TC2_FAULT: IC2.16 (PA15/I15/SERCOM3+4.3); also elsewhere on the board
VBUS: CN1.VBUS
VDDCORE1: C7.1, IC2.29 (VDDCORE)

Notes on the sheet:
Activation Redundancy Processor
Thanks to the design files and hard work done by Adafruit for the Trinket M0
https://cdn-learn.adafruit.com/assets/assets/000/049/778/original/adafruit_products_Adafruit_Trinket_M0.png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 https://github.com/adafruit/Adafruit-Trinket-M0-PCB
KFC-6.1
KREPE Flight Computer
12/15/20
6.1



Board: 4 copper layers, 101.6 x 60.6 mm, 95 parts (9 on the bottom side), 93 nets.

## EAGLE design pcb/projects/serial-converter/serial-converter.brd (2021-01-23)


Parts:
C1, C2, C3, C4: 0.1uF; C0603
C5: 0.01uF; C0603
JP1: PINHD-1X2; 1X02
JP2: PINHD-1X4; 1X04
U$34: MAX3232E; SSOP-16

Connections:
3.3V: C3.1, JP2.2, U$34.16 (VCC)
GND: C2.2, C3.2, C5.2, JP2.1, U$34.15 (GND)
unnamed: C1.1, U$34.1 (C1+)
unnamed: C1.2, U$34.3 (C1-)
unnamed: C4.1, U$34.4 (C2+)
unnamed: C4.2, U$34.5 (C2-)
unnamed: C5.1, U$34.6 (V-)
unnamed: C2.1, U$34.2 (V+)
R232: JP1.2, U$34.8 (RI2)
RIRI: JP2.4, U$34.9 (RO2)
T232: JP1.1, U$34.7 (DO2)
TIRI: JP2.3, U$34.10 (DI2)

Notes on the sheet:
RS232 Connections


Board: 2 copper layers, 22.2 x 9.8 mm, 8 parts (0 on the bottom side), 12 nets.

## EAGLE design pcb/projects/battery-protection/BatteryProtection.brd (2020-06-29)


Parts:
C1: .1uF; 0805
CELL+: MOUNT-PAD-ROUND2.8; 2,8-PAD
CELL-: MOUNT-PAD-ROUND2.8; 2,8-PAD
FET1, FET2: CSD16406Q3; DQG0008A
H2, H3: MOUNT-HOLE2.8; 2,8
PACK+: MOUNT-PAD-ROUND2.8; 2,8-PAD
PACK-: MOUNT-PAD-ROUND2.8; 2,8-PAD
R1: 330; 0603
R2: 2.2k; 0603
U1: BQ29700DSET; DSE6

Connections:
unnamed: C1.1, R1.1, U1.5 (BAT)
unnamed: FET2.4 (GATE), U1.2 (COUT)
unnamed: C1.2, CELL-.B2,8, FET1.1 (SOURCE), U1.4 (VSS)
unnamed: FET1.5 (DRAIN_2), FET2.5 (DRAIN_2)
unnamed: FET1.4 (GATE), U1.3 (DOUT)
unnamed: R2.2, U1.6 (V-)
unnamed: CELL+.B2,8, PACK+.B2,8, R1.2
unnamed: FET2.1 (SOURCE), PACK-.B2,8, R2.1


Board: 2 copper layers, 32.4 x 19.7 mm, 12 parts (0 on the bottom side), 8 nets.

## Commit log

2020-03-30 v1 pcb and documentation
    [kreme-iss.brd, kreme-iss.sch, krepe_iss_v1_digikey_bom.csv]
2020-03-31 created projects folder
    [kreme-iss.brd, kreme-iss.sch]
2020-05-30 update and add battery protection test board
    [BatteryProtection.brd, BatteryProtection.sch]
2020-06-29 v1.1 update
    Updates to the flight computer:
    * update to max31856 tc to digital to support k/j type tc as well as 7
    other types
    * add pins for iridium sbd message ready and iridium actively
    transmitting
    * add capacity sense header
    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
    [BatteryProtection.brd, BatteryProtection.sch, kreme-iss.brd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]
2020-07-01 add fault signal from tc converter
    - add the respective pins to the arduino pinmap
    - update doc pdf and schematic screenshots
    [flight-computer.brd, flight-computer.dxf, flight-computer.sch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]
2020-07-01 add digikey BOM for v1.1
    [flight-computer-v1.1-digikey-bom.csv]
2020-07-04 add activation redundancy processor
    - partial update of documentation to reflect this addition
    - extra diagram of redundant activation
    - pcb update to include a 32 pin qfn samd21 cortex m0 processor and necessary connections to bootload and flash over USB
    [flight-computer.brd, flight-computer.sch]
2020-07-06 updated documentation, BOM and pinmap for activation redundancy processor
    [flight-computer-v1.1-digikey-bom.csv, flight-computer.brd, flight-computer.sch]
2020-07-24 add v1.1 pcb and documentation - added DSP310 barometric pressure sensor - add buzzer - add capacitive sense header - add more interface pins to the safety processor - add arduino pinouts for safety 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
    [flight-computer.brd, flight-computer.sch]
2020-07-24 update v1.1 digikey BOM
    [flight-computer-v1.1-digikey-bom.csv]
2021-01-23 add serial converter files
    [serial-converter.brd, serial-converter.sch]
2021-01-23 add battery protection schematic
2021-01-23 add document revision
    [flight-computer.brd, flight-computer.sch]
2021-03-05 fix wire gauge in fig. 1. add tr-01 testing report
2022-09-16 add initial layout, schematic and libraries for KREPE-2 flight computer revision
    [main_board.brd, main_board.sch]
2022-09-16 updates to layout
    [main_board.brd, main_board.sch]
2022-09-20 update PCB and libraries
    [main_board.brd, main_board.sch]
2022-09-20 silk update
    [main_board.brd]
2022-10-12 added spectrometer breakout
    [spectrometer-shield.brd, spectrometer-shield.sch]
2022-10-12 update libraries and v2 flight comp
    [main_board.brd, main_board.sch]
2022-11-15 v2 cam files, renderings, and datasheets
    [main_board.brd, main_board.sch]
2023-01-03 add ssr to flight computer. add to hardware manual
    [main_board.brd, main_board.sch]
2023-01-13 v2.1 flight computer update. add pressure sensor breakout. add schematic pdfs
    [flight-computer v12.brd, flight-computer v6.sch, pressure-sensor-mux.brd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]
2023-02-14 add battery tabbing spec. cam files for pressure sensor breakout. final schematics for v2.1 as ordered.
    [flight-computer v12.brd, flight-computer v6.sch, flight-computer.brd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]
2024-09-27 add build images and latest schematic from EAGLE
    [flight-computer v12.brd, flight-computer_v6.sch]

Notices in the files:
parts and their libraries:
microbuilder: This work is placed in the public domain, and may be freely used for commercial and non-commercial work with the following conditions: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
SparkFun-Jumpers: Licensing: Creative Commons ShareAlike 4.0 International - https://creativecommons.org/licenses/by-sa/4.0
